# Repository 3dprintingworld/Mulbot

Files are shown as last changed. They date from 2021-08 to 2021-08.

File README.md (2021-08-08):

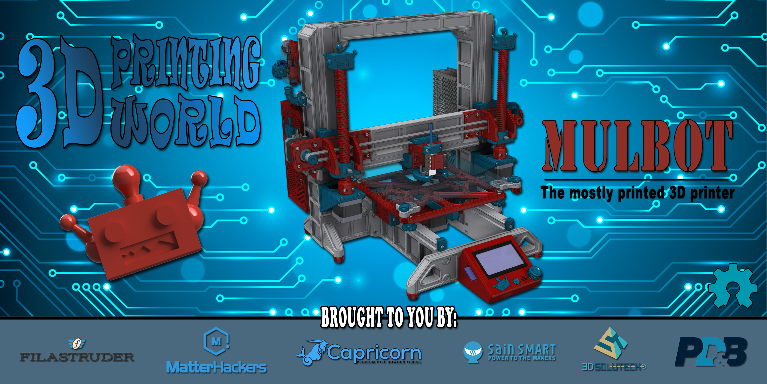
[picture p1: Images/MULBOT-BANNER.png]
Mulbot


The Mulbot is a open source mostly printed printer.

You can find more information at:

Thiniverse: https://www.thingiverse.com/thing:3432384

Facebook User Group: https://www.facebook.com/groups/275718849985834/

Reprap: https://reprap.org/wiki/Mulbot

The Mulbot is a open source mostly printed printer that I designed to bring to show the people at MRRF 2019! 

I had a table for a few hours at MRRF last year and I brought these 3D printed bearings I designed that use recirculating bearing balls and naturally everyone was suggesting that I make a printer with them. By the time I was in the car driving home I already had some ideas in my head and a plan to bring the printer to MRRF the following year!

I figured since the bearings where 3D printed I would print some other parts as well. For example the X-axis uses a 3D printed double wide TPU timing belt and printed drive and Idle pulleys. The Y-axis uses a printed rack and pinion to traverse the bed. The Z-axis is driven by two oversized printed trapezoidal nuts and screws.

Project Goals

MRRF
The main goal for this project was to bring a mostly printed printer that uses the bearings I designed to MRRF 2019!  

The original intent for this project was not to design a printer that others could make. I designed it because I thought it would be fun and that others would like to see it as well! Having said that, I think it’s awesome that so many others want to build it and I will gladly share may ideas with hopes that together as a community we can continue to improve upon the concept.  

The print quality and feasibility of the printer has by far exceed my expectations and I could  not be happy with the way it turned out. I hope this project will push the RepRap concept and perhaps give others ideas on how to make it better. 

Cost Effective? 
My goal was not to make the most cost-effective printer but a mostly printed printer. If you are looking for a really cheap second printer to run production parts, then this printer is probably not the right fit for you.  You can purchase a clone kit cheaper than you can make this printer, as it’s not a goal for this project. Having said that, if you have some filament laying around and some miscellaneous parts, you can make this printer pretty cheaply. 

Self-replicating
As designed the Mulbot is not self-replicating, it was not a goal of mine when I started the project so I did not design for it.  The build volume that is required to print the largest frame members is larger than the printer can print so at this point it’s not self-replicating.  Not to say that it can’t be achieved with some design tweaks.  Honestly, I don’t see the point until a mostly printed printer can perform equally to a manufactured printer. Maybe if we continue to openly share and revise our ideas together as we can make it better! 

Specifications:
Prints PLA and TPU
8-1/2” Square Floating Glass Bed
Print size 
175mm x 200mm x 150mm (dual fan shroud)
145mm x 200mm x 150mm (surround shroud)

Where to Start

Before you undertake this project you may want to consider making one of my other smaller projects first. I would say that printing the Mulbot is no more difficult than any of my other projects, there are just more parts. If you had luck with my other designs you will probably not have an issue the Mulbot. 

Here are some examples that you might want to consider; [Linear bearing][lb], [Stepper slide][ss], [Jack screw][js], [Grippers][grip], [Secret Box][sb]. 

[lb]: https://www.thingiverse.com/thing:2847294
[ss]: https://www.thingiverse.com/thing:2967644
[js]: https://www.thingiverse.com/thing:2219156
[sb]: https://www.thingiverse.com/thing:2977908
[grip]: https://www.thingiverse.com/thing:2204113

Printing  Requirements
Required Print Volume: 250mm x 210mm x 210mm
To print the largest pieces you will need a build volume equal to my Original Prusa MK3. 

Flat Print Surface
I printed all the parts on the Prusa MK3 stock cast aluminum bed with PEI flex plate but it is not perfectly flat.  If I had the choice I would have preferred to print on a glass bed as it would be much flatter. Having said that, because of the way the frame is design I don’t think bed flatness will be a big deal. 

Filament Selection
Everything but the belt and the mounting feet were printed out of PLA, those were printed out of TPU.  I chose PLA because I think it’s the best option as its very stable and doesn’t shrink or warp. I also thought making the printer out of PLA would make it much easier for the vast majority of people to make. 

Note: I did have some softening of the gear pinion and the drive pulley as a result of the heat from the stepper motors so I did end up printing those out of ABS but PETG would probably work as well. 

Test a Bearing First
Before starting to print anything else, I would first print a y-axis bearing rail and bearing. If you can’t get the bearings to work then this will save you from printing the rest of the printer for no reason. The x-axis bearing is the smallest and requires the least amount of filament to print, so I would start there. The bearings need to be the exact otherwise the balls will not recirculate properly. To little preload and the bearing will be to sloppy, too much preload and the balls wont recirculate. See “Bearing Fit” section for more information.

Order the parts
I tried to use suppliers and components that were readily available wherever possible but some components will be better sourced directly from overseas to save money. The biggest case would be for fasteners and hardware. I would start this project by ordering the fasteners and bearing balls needed to build and test at least one bearing so it can be proven and you can move on to printing and building the rest of the machine. 

Filament: 

I used Solutech for all the PLA printed parts. Below is a list of the filament necessary for the color scheme I chose. 

*   1 x [Spool Real Red][RED]
*   2 x [Spool Real White][WHITE]
*   1 x [Spool Real Blue][BLUE]

It takes less then 2kg of filament in total to print the entire printer.

[red]: https://amzn.to/2DqQd2m 
[white]: https://amzn.to/2OreAxD 
[blue]: https://amzn.to/2SPxTEl 

TPU

Sainsmart
*   1 x [Red][RED]
*   2 x [White][WHITE]

Both materials also print great on the non-heated glass bed with a little glue stick.

[white]: https://amzn.to/2QwaF4o 
 [red]: https://amzn.to/2PGZWHo 

Components: 
I designed the printer to use as cost effective components as possible to reduce the cost of the build but to also use some open source components that are reliable and more gooder.  You should be able to build this printer with the components specified in the bom for about $250-300. The cost for fasteners and hardware adds up quick, if you already have some of this stuff in stock you can save some money. 

I have highlighted some of the components below as well as publish a full bom.

Bowden Tubing
*   [Capricorn XC 1.75  Bowden Tubing][cap] 
Since I’ll be printing TPU I went with the original Capricorn XS version with the reduced ID as it will leave less room for the flexible filament to bend. 
[cap]: https://www.captubes.com/shop/#!/1-Meter-XS-Low-Friction-1-75mm-Bowden-Tubing/p/82190682/category=23214267

Hotend
*   [Genuine E3D Lite6 Hot End][hot] 
I thought the Lite6 was a perfect fit for this printer because of its reliability’s and low price tag, around $30. Sure you can order a clone; wait five weeks, maybe save a few bucks, but the loss of quality is just not worth it in my option. Plus I like to support Opensource company’s like E3D because the clones wouldn’t existed without them. You want the 1.75mm Bowden type and the 12v version if your running ramps. 

[hot] https://www.filastruder.com/products/lite6?variant=1227433316

1.75 Bowden Extruder
*   [SeeMeCNC EZR][ezr]

Since the printer doesn’t have a heated bed I thought it would be good to have an extruder that can print both PLA and TPU.  Both materials will print perfectly well with a non-heated glass bed with a little glue stick. The extruder is great at PLA but also at TPU as the filament is better guided through the extruder. What I think makes this extruder most unique is that the pressure roller moves lineally instead of radially on an arm so the pressure stays perpendicular to the path of the filament. You would think that this  would help with flex but at the very least it’s a cool design. 

The other thing that is cool is since SeeMeCNC is an open source company I was able to down load the actually 3D models of the extruder from their GitHub page! This made life so easy when it came to design for the extruder. The other thing is its only $35 which is almost half other extruders on the market which makes it perfect for this printer. You don’t even have to worry about it causing you inconsistent extrusion. :) Additionally SeeMeCNC is also a major sponsor at MRRF, which is a plus.

[ezr}: https://www.matterhackers.com/store/l/seemecnc-ezrstruder-kit/sk/MWHJ83XV?aff=7457

Fasteners

See the BOM for a full list of fasteners

Hex Nuts
*    70 X M3 x 0.5 
*    10 X M4 x 0.7 
I also used square nuts where applicable 

Button Head Cap Screws
*    4 X M3 x 0.5 x 6MM LG. 

Flat Head Cap Screws
*    4 X M3x0.5 x 50MM LG. 

Socket Head Set Screws
*    2 X M3x0.5 x 5MM LG. 
*    4 X M3X0.5 X 12MM LG. 

Socket Head Cap Screw
*    15 X M3x0.5 x 6MM LG. 
*    9 X M3x0.5 x 8MM LG. 
*    46 X M3x0.5 x 10MM LG. 
*    40 X M3x0.5 x 16MM LG. 
*    13 X M3x0.5 x 20M LG. 
*    2 X M3x0.5 x 35MM LG. 
*    7 X M4x0.7 x 10MM LG. 
*    1 X M4x0.7 x 12MM LG. 
*    26 X M4x0.7 x 20MM LG.

Hardware
Bed Springs
*    Aliexpress:  4  X [7.5MM OD X 20M LG X 1.2MM Wire Compression Spring][spring]

Bearing Balls
*    Ebay: 572 X  [GRADE 100 4.5MM S.S. Bearing Balls][balls]
Must  be Grade 100 bearing balls. BB's or shot will not work!

*    Build Surface: Glass 8.5” x 8.5” x .12”d

[spring]: https://www.aliexpress.com/item/10pcs-Leveling-Spring-Accessories-for-3D-Printer-Extruder-Heated-Bed-Ultimaker-Makerbot/32880868017.html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
[balls]: https://www.ebay.com/itm/300-pcs-4-5mm-0-1772-Inch-SS316-Stainless-Steel-Bearing-Ball-316-G100/301149470266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

Thread Inserts
You will need a soldering iron for inserting the heat-set inserts.  You can use a standard soldering tip but the custom tip linked below is much better at inserting the nut straight.  It’s also nice to have a soldering iron with adjustable temperature so you can turn it down really low. If it’s too hot PLA will get to soft very quickly which could ruin the hole. I install my inserts at 350F, which gives a little time for the nut to heat up and sink in. 

*   [M3 Tread Inserts][m3]
*   [M4 Tread Inserts][m4]
*   [Heat-Set Install Tip][tip]

[m3]: https://amzn.to/2Fm3Way
[m4]: https://amzn.to/2Xj3ikD
[tip]: https://amzn.to/2FlXl01

Control System

I chose a ramps 1.4 controller as it’s the cheapest, most available controller.

*   Sainsmart: [Ramps 1.4 & Mega Controller][sain] 
I went with DRV8825 drivers because I read that they run cooler but A4988’s would work as well. 
[sain]: http://shrsl.com/1be01

*   Amazon: [Rep Rap Discount Full Graphic Smart Display][dis] 
 [dis]: https://amzn.to/2GttCn7

*   Amazon: [Limit Switch][ls] 
Make sure you don’t wire these backwards.  If you do you will blow the 5v on our mega because of the led, I learned the hard way…
[ls]: https://amzn.to/2Gw5iB8

*   Amazon:[Nema 17 Stepper Motors][step]  
I just went with the cheapest motors I could find. 
[step]: https://amzn.to/2BJ3LUd

*   Amazon:[5015 Blower Fan, 12v][fan]  
[fan]: https://amzn.to/2EIfZyn

You will also need a 90 USB A Male to B Male cable for connecting to the Arduino. 

LED’s
*   Amazon: [5630 12v LED Strip Lights][led] 
I designed for two 5630 12v LED strip lights with adhesive backing. There is a spot for two strips which allow you space to run the wiring into the frame. One strip gets installed on the x-axis rail and one on the top crossmember. I powered the led’s on the x-axis rail from the ramps board and ran the led on the top crossmember directly to the power supply. This way both led’s turn on when the power supply is switched on. 
[led]: https://amzn.to/2TiFu1u

Power Supply
*   Amazon: [150W 12V Power Supply][ps]
Since there is not a headed bed you can get away with a smaller power supply, this one is really cheap.  If you want the ability to update to a heated bed you will need a larger power supply.  If you go with this power supply though the mounting holes and the cover will all match up. 
[ps]: https://amzn.to/2Erzmf1

Inlet Plug 5A with Switch
*   Amazon: [IEC320][plug]
[plug]: https://amzn.to/2XvJn1Y

Printing

Orientation & Supports
The parts should be in the correct scale and orientation when you bring them into your slicer. None of the parts require supports with the exception of the y-axis servo mount which needs some supports for the slotted holes for the stepper motor. 

Material’s
I printed all the parts out of PLA with the exception of the timing belt, which is TPU.  After running it for a while I noticed that the screws would loosen up on the pinion and the drive pulley as a result of heat from the steppers.  I ended up printing those in ABS, but PETG would probably be a good choice as well. If you are printing them out of ABS you will have to scale it up slightly to account for shrinkage. 

Lifting
I also had issues with some of the large frame members lifting off the bed.  I normally don’t have this issue but it’s because the parts are so narrow and tall it’s hard to keep them on the bed even with a brim. As a result I used very large helper discs on the ends of the frames to keep them down while printing which did the trick.

Shells and Infill
I printed the entire printer with less than 2 kg of filament! Pretty much all the parts were printed with only 2 shells and 15% infill with the exception of the screws.  The screws were printed with four shells and 25% infill to make them more ridged. If you are wondering why they are hollow it’s because it makes them much stiffer. 

Since this was my first time printing it I did not want to waste a lot of filament in case I needed to make revisions so I did not make the parts really strong.  However, all the parts seem plenty strong with these settings. If you wanted to make it stronger you could try 3-4 shells with 20-25% infill but I feel any more than that would be overkill. 

Bearing Assembly
Bearing Preload
Hopefully everyone’s bearings will have just the right amount of preload, but not everyone’s printer will be the same so this probably is not going to happen... I would say the relationship between the rails and the bearing need to be within +/- .005” to function properly. If your preload is not right you can try scaling the Y axis(as the model comes in your slicer) slightly to compensate. I would try scaling it up or down roughly .7% which would equate to .005”.  

Bearing Balls
The bearing are designed to utilize Grade 100 4.5mm S.S. bearing balls, it will not work with standard BB’s.  Bearing balls are more expensive then BB’s but they are also much more accurate and result in a smoother running bearing. I think BB’s would have worked but I thought a smoother bearing was worth the extra $10. Each bearing takes 112 bearing balls.

He is a quick video showing the assembly of the original bearings.
Bearing assembly video https://youtu.be/cF8fXATjccQ

Cleanup and Deburr
Burrs and unsmooth print surfaces will affect your bearings performance.  I have noticed that the bearings run a little rough at first but get smother as they break in.  I believe this is a result of the endcaps not being smoothed and/or having burrs.  Make sure the balls can freely flow thru each return track and end cap by manually dropping a single bearing in each hole. After the bearings have been broken in I have not noticed any issues with wearing. 

Preload
The bearing preload is not as crucial on the Y and Z axis as it is on the X axis.  The Y and Z axis both have two bearings instead of one and they hardly have any overhung load so they can get away with more slop. The hot end is overhung on the X axis bearing, plus there is only one bearing, so you will need a good amount of preload to remove the slop and have the extruder held properly. 

Y-Axis and Bed Assembly
I would start the assembly by first putting the bearings on both y-axis rails. Then build the rest of the y-axis frame assembly but only finger tighten the screws.  After the frame is assembled mount the bed frame on the bearings but don’t install the stepper motor yet.  Place the frame on a flat surface and tighten all the screws as you move the bed back and forth. Last install the servo motor and drive pinion.  Use the slotted holes and set screws to remove the clearance between the gear rack and pinion.

Credit to [Komb]{komb} for the rack and Pinion
[knob]: https://www.thingiverse.com/thing:173516

X and Z-Axis Frame Assembly
Mount the two Z-axis bearing and the X-axis bearing to their corresponding bearing rail. Attach the Z-Axis frame components to the Y-axis frame that was just assembled.  Connect the X-axis frame rail to the two Z-axis bearings and move the Z-axis up/down and tighten all the mounting screws.  Lastly add the drive components for both the X and Z axis. 

The X-axis idle pulley uses the same 4.5mm bearing balls that the linear bearings use.

Cooling Nozzle
Choosing a Part Cooling Nozzle

There are two options when choosing a hot end and part cooling fan. One option is to use a 40mm dual fan shroud like the one that [eiPionezero][fan] made that mounts directly to the lite6 heatsink. The other option is to use the fan that comes with the hotend along with a separate 5015 blower and surround shroud for better part cooling.  

The surround shroud cools really well but the down side is that it reduces the build volume as the shroud will run into the bed clips as they are above the glass. See “specifications” for more information.  As a result I made a spacer that attaches to the x-axis switch arm that reduces the travel when using the surround nozzle. 

[fan]: https://www.thingiverse.com/thing:839620

Controller & Firmware
I am running [Marlin][mar] on the ramps board which I really like and was a lot of fun to configure! I have not posted my configuration files as I am not a expert at setting them up but if it will help some people out I would be happy to do so, just let me know. 

I did configure for “EFF”, since I do not have a heated bed.  This way you can use D8 to control your hotend fan so that it automatically turns on/off.  Just remember to supply voltage to both 5a and 11a input terminals. 

[mar]:http://marlinfw.org/

VREF
I adjusted the Vref Voltage on each of my DRV8825 drivers and it really helped to reduce the heat of the steppers. I was able to adjust the voltage down quite a bit and still not have any missed steps.  I think it’s a result that everything is so light since it’s all made of plastic. 

Maintenance
Lubrication 
I have not lubricated any of the printed components because I did not want the mess but I would imagine that it would greatly increase the life cycle of the components.  I would recommend using [PTFE Supper Lube][lube] on the rack, pinion, and the screws. I designed for grease zerks in the Z-axis nuts but I have not used them yet. I installed the press fit grease zerk using a soldering iron like a heat-sink thread insert. 

I have not tried lubrication on the recirculating bearings yet.  I did try some PTFE spray on the single row version and it caused the ball to not recirculate properly so I have not experimented with it since. 

[lube]: https://amzn.to/2Tc7VPi

Printed Belt
The TPU printed belt works surprisingly well.  Since there is no tension members it will stretch but my calibration cube was still pretty accurate. I did notice that if I left the belt under tension for a while it has some memory and it causes a hump in the belt where its being bent around the pulleys.  After running it a while the hump will work itself out, but as a result when I’m not using it I try to release the tension so I don’t have this issue. 

Resources
*   [Prusa Step Calculator][cal]
Use this to calculate the steps per axis.  The default steps in marlin were actually a good starting point, I just adjusted from there. 
*   [Marlin][mar]
Firmware

[cal]: https://www.prusaprinters.org/calculator/
[mar]: http://marlinfw.org/

Closing and Moving Forward
This was a really great project and I’m so happy that I took it on! How this project moves forward will be based on the community’s feedback. If a lot of people want to build it and have ideas on how to make it better I would be happy to start a gethub page so we can better share and organize our ideas. If we all put our ideas together I know we can make it even better.  I look forward to receiving your feedback and how you would like to see the project proceed. 

Hardware Kits
The other thing that is kind of a pain is sourcing the fasteners and other hardware. If there is enough interest I can purchase a large quantity of hardware and sell it as a kit which will save people time and money.  If this is something you are interested in let me know in the comments, if I enough people are interested I can get a large order started. 

Sponsors

###3D Printing World and the Mulbot will be at MRRF 2019!  Thanks to our sponsors for providing the components necessary to bring a finished Mulbot to show everyone at MRRF this year! Hope to see you there!

*   [Capricorn][cap]
*   [Fiastruder][fil]
*   [Matterhackers][mat]
*   [Sainsmart][san]
*   [Solutech][sol]

A special thanks to Filastruder and E3D for sponsoring a table for the printer at the festival this year!

[cap]: https://www.captubes.com/
[fil]: https://www.filastruder.com/
[mat]: https://www.matterhackers.com/?aff=7457
[san]: https://www.sainsmart.com/
[sol]: http://www.3dsolutech.com/

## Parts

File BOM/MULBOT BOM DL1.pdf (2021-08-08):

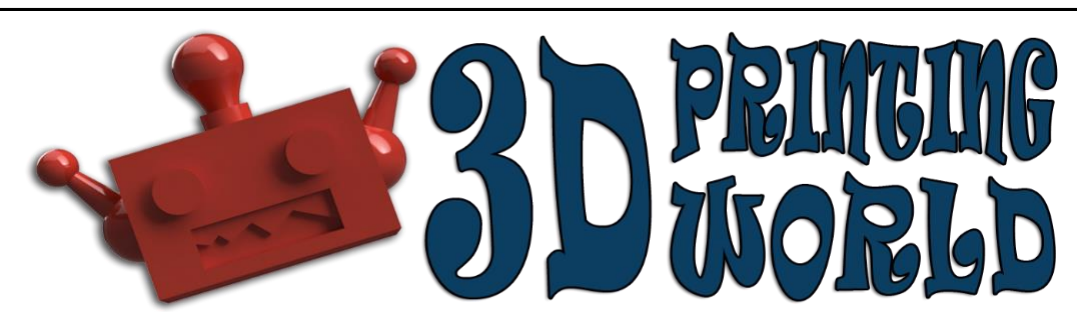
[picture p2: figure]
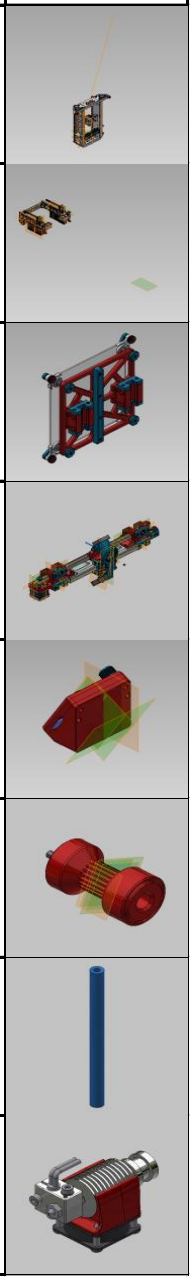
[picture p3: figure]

Item | QTY | Part Number | Description | Vendor | Thumbnail
1 | 1 | DL1-01 | Y-AXIS FRAME | 3DPW
2 | 1 | DL1-02 | Z-AXIS FRAME | 3DPW
3 | 1 | DL1-03 | BED ASSEMBLY | 3DPW
4 | 1 | DL1-04 | X-AXIS ASSEMBLY | 3DPW
5 | 1 | DL1-05 | DISPLAY ASSEMBLY | 3DPW
6 | 1 | DL1-06 | IDLER ASSEMBLY | 3DPW
7 | 1 | 1001 | XS BOWDEN TUBING | CAPRICORN
8 | 1 | V6 LITE 1.75MM | GENUINE E3D BOWDEN HOT END | FILASTRUDER

## Mulbot DL1 BOM

9 | 1 | EZR | EXTRUDER | MATTERHACKERS
10 | 2 | 1102K520 | DRIVE-IN ZERT | MCMASTER
11 | 57 | 94180A331 | M3 HEAT SET THREAD INSERT | MCMASTER
12 | 9 | 94180A351 | M4 HEAT SET THREAD INSERT | MCMASTER
13 | 1 | 1.4 | RAMPS | SAINSMART
14 | 1 | 1.4 | RAMP BOARD | SAINSMART
15 | 1 | 1.4 ADAPTOR | DISPLAY ADAPTOR | SAINSMART
16 | 6 | DL1-02-08 | MOUNTING FOOT, TPU | SAINSMART
17 | 3 | LS | LIMIT SWITH | SAINSMART
18 | 1 | REPRAP | DISCOUNT DISPLAY | SAINSMART

19 | 1 | Y-BELT | TPU, X-AXIS BELT | SAINSMART
20 | 1 | DL1-01-01 | Y-AXIS, LEFT FRAME RAIL | SOLUTECH
21 | 1 | DL1-01-02 | Y-AXIS, RIGHT FRAME RAIL | SOLUTECH
22 | 1 | DL1-01-03 | Y-AXIS, FRONT CONECTOR | SOLUTECH
23 | 1 | DL1-01-04 | Y-AXIS. BACK CONNECTOR | SOLUTECH
24 | 1 | DL1-01-05 | WIRE WAY | SOLUTECH
25 | 4 | DL1-01-06 | Y-AXIS, ENDSTOP | SOLUTECH
26 | 1 | DL1-01-07 | Y-AXIS, MOTOR MOUNT | SOLUTECH
27 | 1 | DL1-01-09 | Y-AXIS, DRIVE GEAR | SOLUTECH
28 | 1 | DL1-02-01 | Z-AXIS RAIL, LEFT | SOLUTECH

29 | 1 | DL1-02-02 | Z-AXIS RAIL, RIGHT | SOLUTECH
30 | 1 | DL1-02-03 | CROSS FRAME, LEFT | SOLUTECH
31 | 1 | DL1-02-04 | CROSS FRAME, RIGHT | SOLUTECH
32 | 1 | DL1-02-05 | Z-AXIS, CROSS BAR | SOLUTECH
33 | 2 | DL1-02-06 | Z-AXIS, ACREW | SOLUTECH
34 | 2 | DL1-02-07 | Z-AXIS, MOTOR MOUNT | SOLUTECH
35 | 1 | DL1-02-09 | RAMPS ENCLOSURE | SOLUTECH
36 | 1 | DL1-02-10 | RAMPS DOOR | SOLUTECH
37 | 1 | DL1-02-11 | LARGE ROBOT HEAD | SOLUTECH
38 | 1 | DL1-02-12 | WIRE STRAIN, COVER | SOLUTECH

39 | 1 | DL1-02-13 | WIRE STRAIN, MOUNT | SOLUTECH
40 | 1 | DL1-02-14 | ROBOT HEAD SPINNER | SOLUTECH
41 | 1 | DL1-02-15 | POWER SUPPLY, GUARD | SOLUTECH
42 | 1 | DL1-02-16 | EXTRUDER MOUNTING BRACKET | SOLUTECH
43 | 2 | DL1-03-01 | Y-AXIS, CARRIAGE | SOLUTECH
44 | 9 | DL1-03-02 | BEARING CAP | SOLUTECH
45 | 1 | DL1-03-03 | Y-AXIS, GEAR RACK | SOLUTECH
46 | 1 | DL1-03-04 | BED SUPPORT | SOLUTECH
47 | 4 | DL1-03-05 | LEVELING KNOB | SOLUTECH
48 | 4 | DL1-03-06 | GLASS CORNER LOCATOR | SOLUTECH

49 | 4 | DL1-03-07 | GLASS CLAMP | SOLUTECH
50 | 4 | DL1-03-08 | CORNER THREAD | SOLUTECH
51 | 1 | DL1-04-01 | Z-AXIS, LEFT CARRIAGE | SOLUTECH
52 | 1 | DL1-04-02 | Z-AXIS, RIGHT CARRIAGE | SOLUTECH
53 | 1 | DL1-04-03 | HOT END CARRIAGE | SOLUTECH
54 | 1 | DL1-04-04 | X-AXIS BEARING RAIL | SOLUTECH
55 | 1 | DL1-04-05 | LIMIT EXTENDER | SOLUTECH
56 | 2 | DL1-04-06 | Z-AXIS NUT | SOLUTECH
57 | 1 | DL1-04-07 | HOT END CLAMP | SOLUTECH
58 | 1 | DL1-04-08 | DRIVE PULLEY | SOLUTECH

59 | 1 | DL1-04-09 | X-AXIS, BELT CLAMP | SOLUTECH
60 | 1 | DL1-04-10 | TAKE UP BRACKET | SOLUTECH
61 | 1 | DL1-04-11 | IDLER TAKE UP PLATE | SOLUTECH
62 | 1 | DL1-04-12 | TAKE UP KNOB | SOLUTECH
63 | 1 | DL1-04-13 | X-AXIS, BEARING CAP W/SWITCH | SOLUTECH
64 | 1 | DL1-04-15 | COOLING NOZZLE | SOLUTECH
65 | 1 | DL1-05-01 | CONTROLLER BOTTOM | SOLUTECH
66 | 1 | DL1-05-02 | CONTROLLER TOP | SOLUTECH
67 | 1 | DL1-05-03 | RESET BUTTON | SOLUTECH
68 | 1 | DL1-05-04 | CONTROL KNOB | SOLUTECH

69 | 3 | DL1-05-05 | MINI ROBOT HEAD | SOLUTECH
71 | 1 | DL1-06-01 | IDLE PULLEY | SOLUTECH
72 | 1 | DL1-06-02 | IDLER SHAFT, A | SOLUTECH
73 | 1 | DL1-06-03 | IDLER SHAFT, B | SOLUTECH
74 | 2 | DL1-06-04 | BEARING CAGE | SOLUTECH
75 | 1 | .13" X 8" X 8" | GLASS BED
76 | 1 | 5015 | BLOWER, 12VDC
77 | 4 | 7.5MM OD X 20M LG X 1.2MM WIRE COMPRESSION SPRING
78 | 572 | GRADE 100 | 4.5MM S.S. BEARING BALLS
79 | 70 | M3 x 0.5 | Hex Nut

80 | 4 | M3 x 0.5 x 6 | BHCS
81 | 46 | M3x0.5 x 10 | SHCS
82 | 40 | M3x0.5 x 16 | SHCS
83 | 13 | M3x0.5 x 20 | SHCS
84 | 2 | M3x0.5 x 35 | SHCS
85 | 2 | M3x0.5 x 5 | HHSS
86 | 4 | M3x0.5 x 50 | FHCS
87 | 15 | M3x0.5 x 6 | SHCS
88 | 9 | M3x0.5 x 8 | SHCS
89 | 4 | M3X0.5 X12 | SHSS

90 | 10 | M4 x 0.7 | Hex Nut
91 | 7 | M4x0.7 x 10 | SHCS
92 | 1 | M4x0.7 x 12 | SHCS
93 | 26 | M4x0.7 x 20 | SHCS
94 | 5 | NEMA 17 | STEPPER MOTOR
95 | 1 | RS-150-2 | POWER SUPPLY, 150W, 12V
96 | 1 | 5630 | LED STRIP, 12V WHITE

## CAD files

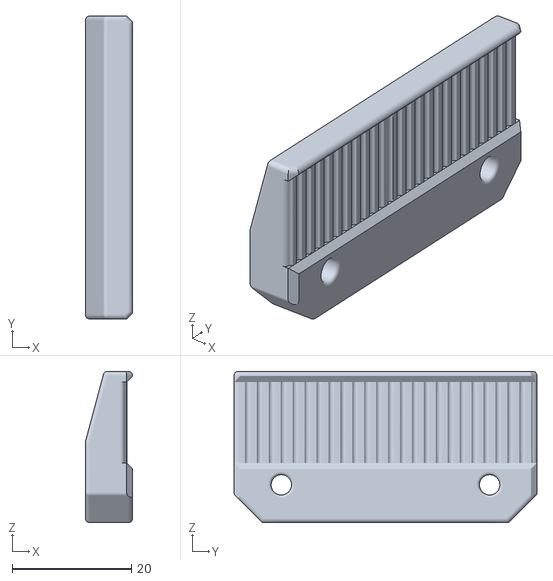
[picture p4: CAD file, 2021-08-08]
MODELS/DL1-04-09.stl
7.94 x 50.8 x 25.4

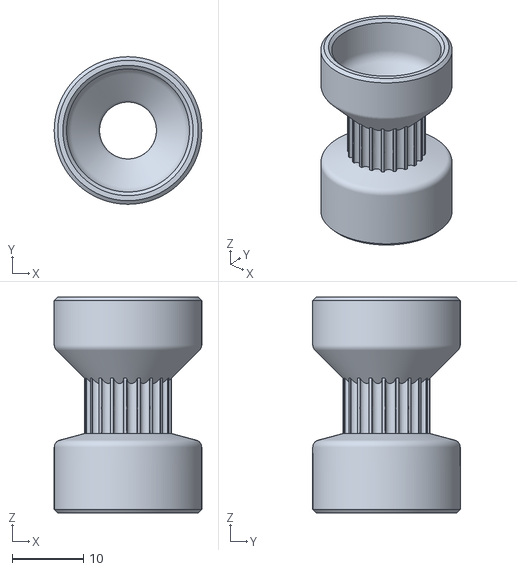
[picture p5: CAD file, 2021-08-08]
MODELS/DL1-06-01-6MM.stl
20.6 x 20.6 x 30.2

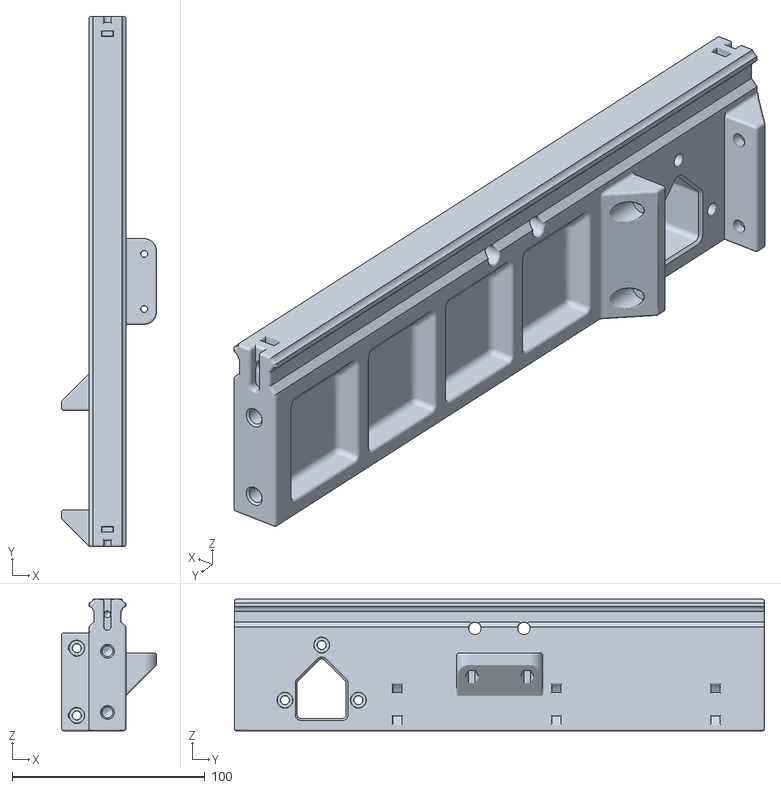
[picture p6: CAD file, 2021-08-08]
MODELS/DL1-01-02.stl
49.2 x 275.0 x 68.3

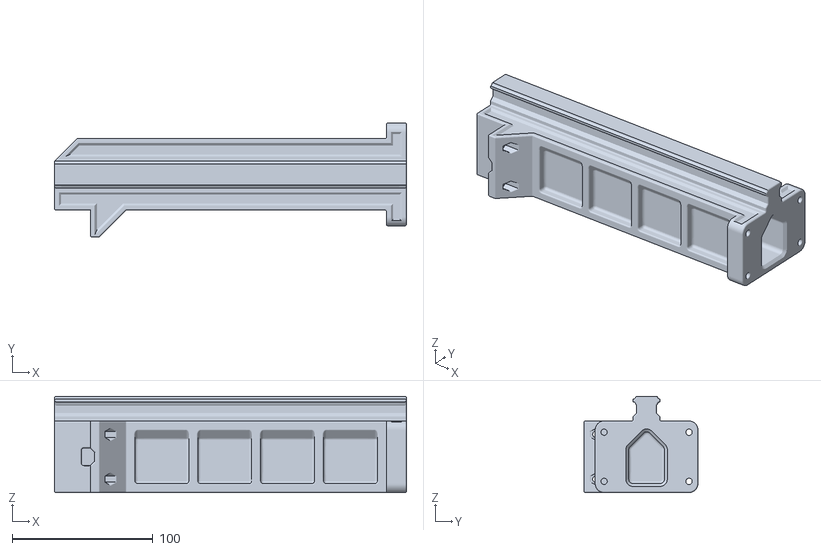
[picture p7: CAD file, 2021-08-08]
MODELS/DL1-02-02.stl
250.0 x 81.0 x 68.3

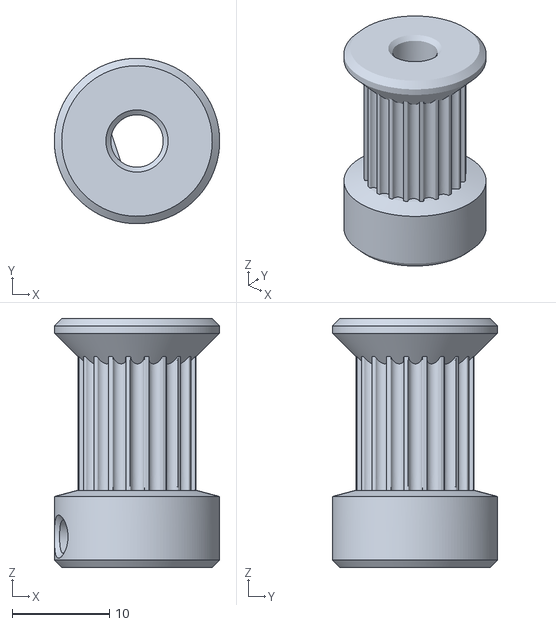
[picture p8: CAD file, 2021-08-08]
MODELS/DL1-04-08.stl
17.0 x 17.0 x 25.6

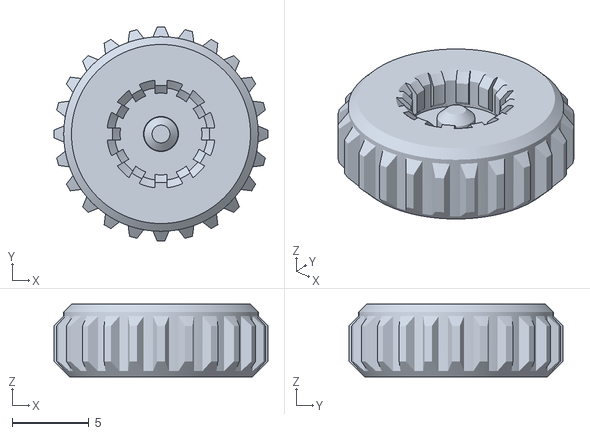
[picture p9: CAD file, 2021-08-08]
MODELS/DL1-04-17.stl
14.0 x 14.0 x 4.76

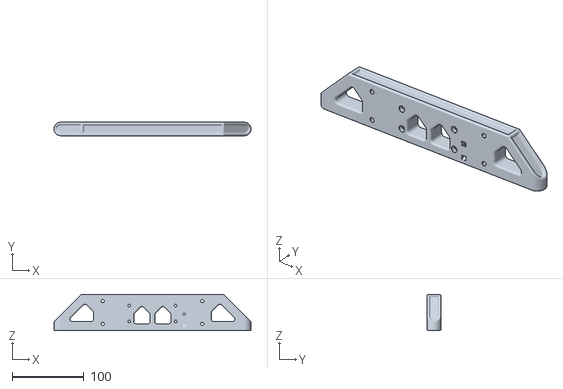
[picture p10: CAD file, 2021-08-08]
MODELS/DL1-01-03.stl
275.0 x 19.1 x 50.8

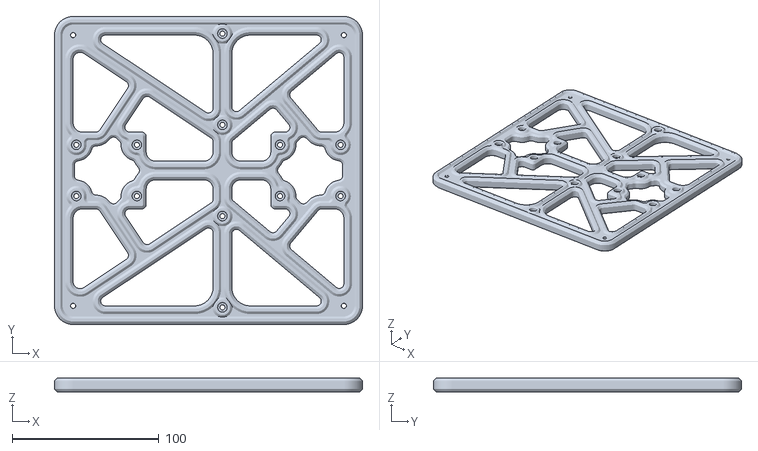
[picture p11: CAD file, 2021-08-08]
MODELS/DL1-03-04.stl
210.0 x 210.0 x 9.52

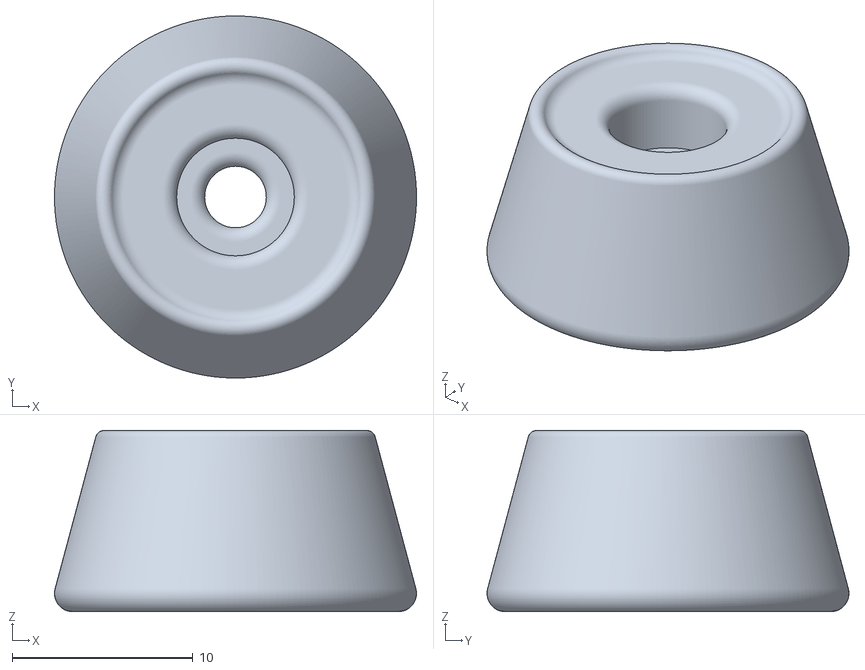
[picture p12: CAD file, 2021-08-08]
MODELS/DL1-01-08.stl
20.0 x 20.0 x 10.0

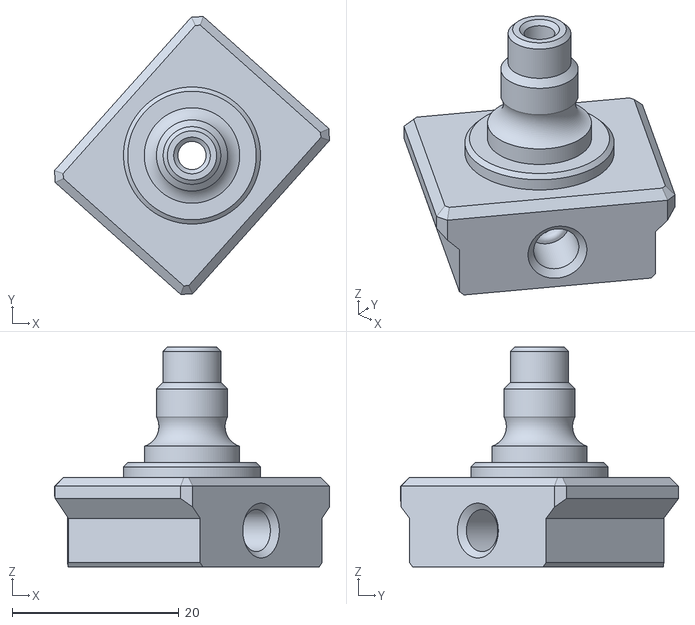
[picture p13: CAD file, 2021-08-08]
MODELS/DL1-06-03-6MM.stl
33.0 x 33.4 x 26.4

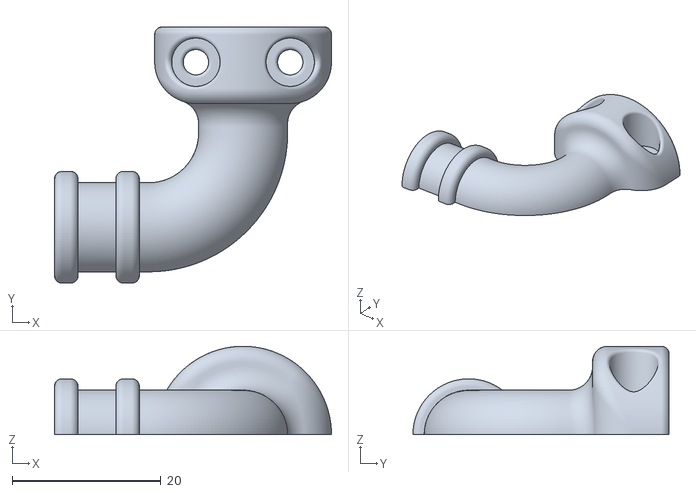
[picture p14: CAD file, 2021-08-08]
MODELS/DL1-02-12.stl
37.3 x 34.5 x 11.9

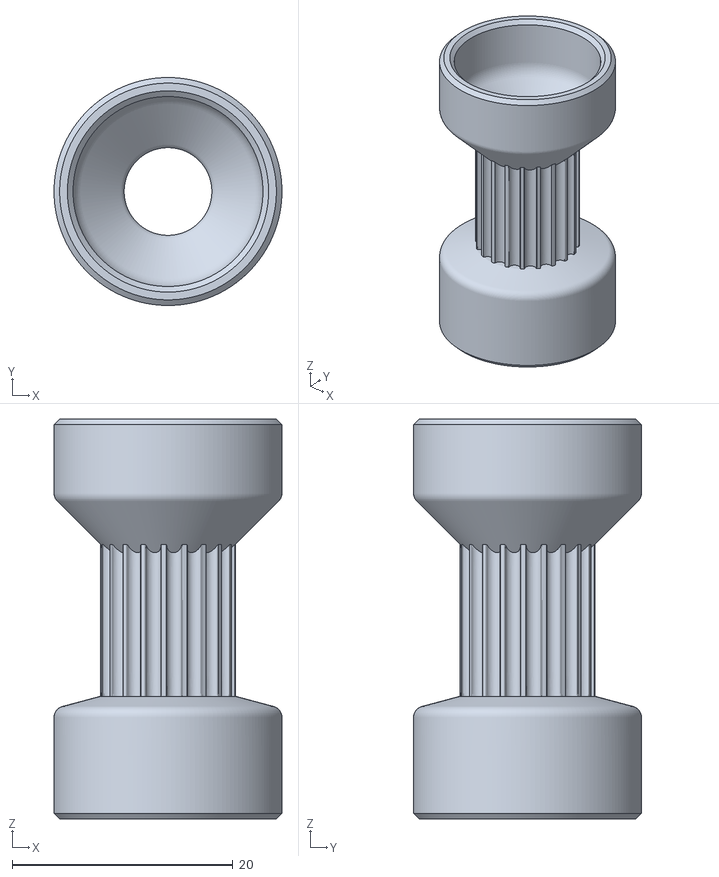
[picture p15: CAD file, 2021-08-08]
MODELS/DL1-06-01.stl
20.6 x 20.6 x 36.2

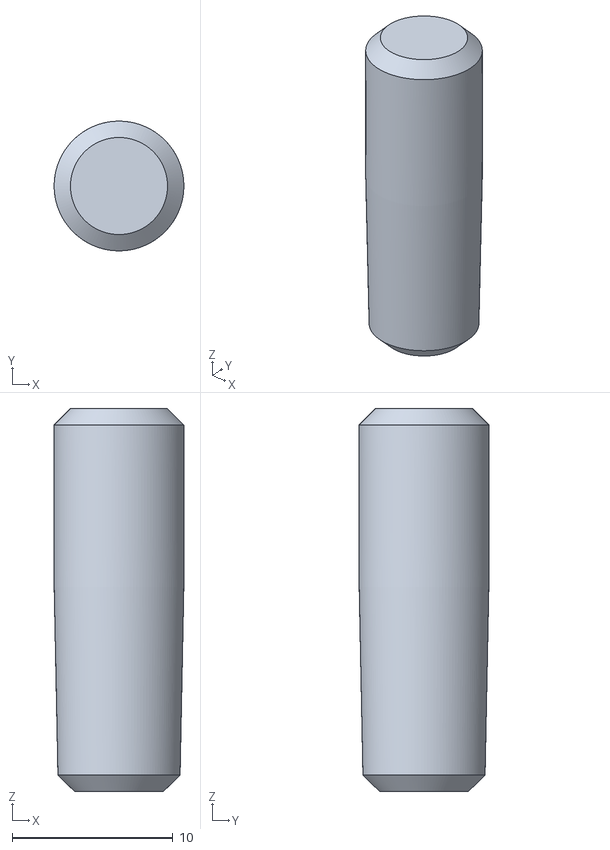
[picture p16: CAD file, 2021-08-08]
MODELS/DL1-02-18.stl
8.06 x 8.06 x 23.8

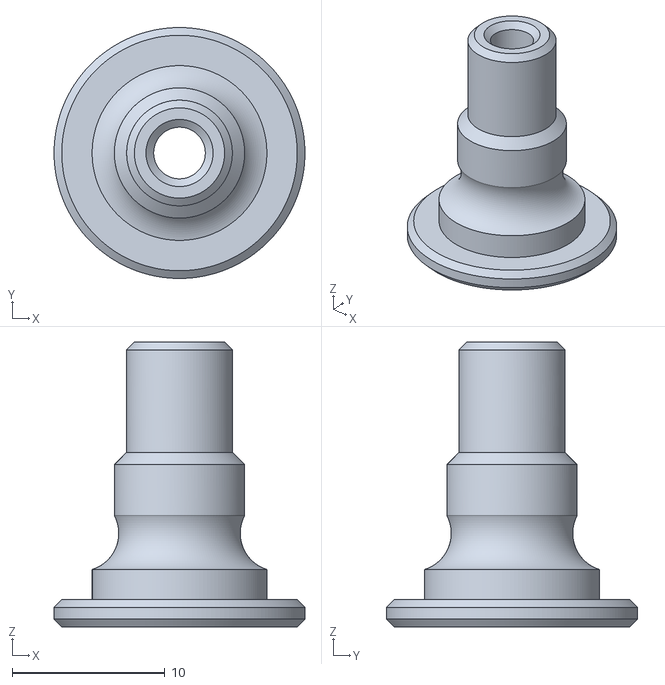
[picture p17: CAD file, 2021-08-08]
MODELS/DL1-06-03.stl
16.4 x 16.4 x 18.7

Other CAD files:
MODELS/DL1-05-01.stl
MODELS/DL1-04-07.stl
MODELS/DL1-06-03_REVB.stl
MODELS/DL1-03-02.stl
MODELS/DL1-01-01.stl
MODELS/DL1-01-04.stl
MODELS/DL1-01-06.stl
MODELS/DL1-01-07.stl
MODELS/DL1-01-09.stl
MODELS/DL1-02-03.stl
MODELS/DL1-02-04.stl
MODELS/DL1-02-05.stl
MODELS/DL1-02-07.stl
MODELS/DL1-02-11.stl
MODELS/DL1-02-13.stl
MODELS/DL1-02-14.stl
MODELS/DL1-02-15.stl
MODELS/DL1-02-16.stl
MODELS/DL1-02-17.stl
MODELS/DL1-03-01.stl
MODELS/DL1-03-03.stl
MODELS/DL1-03-05.stl
MODELS/DL1-03-06.stl
MODELS/DL1-03-07.stl
MODELS/DL1-03-08.stl
MODELS/DL1-04-01.stl
MODELS/DL1-04-02.stl
MODELS/DL1-04-03_HEAVY PRELOAD.stl
MODELS/DL1-04-03_LIGHT PRELOAD.stl
MODELS/DL1-04-04.stl
MODELS/DL1-04-05.stl
MODELS/DL1-04-06.stl
MODELS/DL1-04-08-6MM.stl
MODELS/DL1-04-10.stl
MODELS/DL1-04-10_REVB.stl
MODELS/DL1-04-11.stl
MODELS/DL1-04-12.stl
MODELS/DL1-04-13.stl
MODELS/DL1-04-16.stl
MODELS/DL1-05-02.stl
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
